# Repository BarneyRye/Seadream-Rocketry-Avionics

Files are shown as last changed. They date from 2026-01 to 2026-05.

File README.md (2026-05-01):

# Seadream Rocketry PCB and Code
 
 | Kicad files include schematic, pcb, extra symbols, footprints 3d files and also the production files for JLCPCB |
 |---------|
 | Included code written in Platform.io on VSCode, uses prebuilt libaries and freeRTOS, one task for sensor reading and audio, other task for writing to SD |

 *Exclaimer: Component libraries only usable on KiCAD 9!* </br></br>

 Follow us on [Instagram](https://www.instagram.com/seadreamrocketry/)

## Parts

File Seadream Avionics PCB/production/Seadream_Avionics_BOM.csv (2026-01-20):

Reference | Qty | Value | DNP | Exclude from BOM | Exclude from Board | Footprint | Datasheet | Description | Part NO.
C1,C3,C4,C5,C6,C7,C12,C13,C14 | 9 | 100nF |  |  |  | Capacitor_SMD:C_0402_1005Metric | https://jlcpcb.com/api/file/downloadByFileSystemAccessId/8579707269996871680 | CL05B104KO5NNNC | C1525
C2,C8,C9,C10 | 4 | 10uF |  |  |  | Capacitor_SMD:C_0603_1608Metric | https://jlcpcb.com/api/file/downloadByFileSystemAccessId/8579707107920437248 | CL10A106KP8NNNC | C19702
C11 | 1 | 22uF |  |  |  | Capacitor_SMD:C_0805_2012Metric | https://jlcpcb.com/api/file/downloadByFileSystemAccessId/8579706866429190144 | CL21A226MAQNNNE | C45783
C15 | 1 | 1uF |  |  |  | Capacitor_SMD:C_0402_1005Metric | https://jlcpcb.com/api/file/downloadByFileSystemAccessId/8579707174974914560 | CL05A105KA5NQNC | C52923
D1,D2,D3 | 3 | LED |  |  |  | LED_SMD:LED_0805_2012Metric | https://jlcpcb.com/api/file/downloadByFileSystemAccessId/8550724080677908480 | NCD0805R1 | C84256
J1,J3 | 2 | B2B-PH-K-S(LF)(SN) |  |  |  | Connector_JST:JST_PH_B2B-PH-K_1x02_P2.00mm_Vertical | https://jlcpcb.com/api/file/downloadByFileSystemAccessId/8588889744620572672 | B2B-PH-K-S(LF)(SN) | C131337
J2 | 1 | TYPE-C16PIN |  |  |  | 2FOOTPRINTS:SHOUHAN_TYPE-C_16PIN_2MD__073_ | https://jlcpcb.com/api/file/downloadByFileSystemAccessId/8588893971980423168 | TYPE-C16PIN | C393939
MICRO_SD1 | 1 | TF-01A |  |  |  | 2FOOTPRINTS:TF-01A | https://jlcpcb.com/api/file/downloadByFileSystemAccessId/8588894212661764096 | TF-01A | C91145
R1,R2,R11 | 3 | 10k |  |  |  | Resistor_SMD:R_0402_1005Metric | https://jlcpcb.com/api/file/downloadByFileSystemAccessId/8588881989415931904 | 0402WGJ0103TCE | C25531
R3,R4 | 2 | 4k7 |  |  |  | Resistor_SMD:R_0402_1005Metric | https://jlcpcb.com/api/file/downloadByFileSystemAccessId/8579705941367193600 | 0402WGF4701TCE | C25900
R5 | 1 | 330 |  |  |  | Resistor_SMD:R_0603_1608Metric | https://jlcpcb.com/api/file/downloadByFileSystemAccessId/8579706223213461504 | 0603WAF3300T5E | C23138
R7,R10 | 2 | 5k1 |  |  |  | Resistor_SMD:R_0402_1005Metric | https://jlcpcb.com/api/file/downloadByFileSystemAccessId/8579706036003409920 | 0402WGF5101TCE | C25905
R8,R9 | 2 | 220 |  |  |  | Resistor_SMD:R_0603_1608Metric | https://jlcpcb.com/api/file/downloadByFileSystemAccessId/8579706178210742272 | 0603WAF2200T5E | C22962
S1 | 1 | KMR221GLFS |  |  |  | 2FOOTPRINTS:SW_KMR221GLFS | https://jlcpcb.com/api/file/downloadByFileSystemAccessId/8588916370310369280 | KMR221GLFS | C72443
SW1 | 1 | SSSS810701 |  |  |  | 2FOOTPRINTS:SW-SMD_SSSS810701 | https://jlcpcb.com/api/file/downloadByFileSystemAccessId/8588917637593751552 | SSSS810701 | C97433
U1 | 1 | BMP280 |  |  |  | 2FOOTPRINTS:XDCR_BMP280 | https://jlcpcb.com/api/file/downloadByFileSystemAccessId/8588881905890156544 | BMP280 | C83291
U2 | 1 | ESP32-S3-MINI-1U-N8 |  |  |  | RF_Module:ESP32-S2-MINI-1U | https://documentation.espressif.com/esp32-s3-mini-1_mini-1u_datasheet_en.pdf | ESP32-S3-MINI-1U-N8 | C2980299
U3 | 1 | LSM6DSO32TR |  |  |  | 2FOOTPRINTS:XDCR_LSM6DSO32TR | https://jlcpcb.com/api/file/downloadByFileSystemAccessId/8588926227138138112 | LSM6DSO32TR | C1864162
U4 | 1 | LD1117S33TR |  |  |  | 2FOOTPRINTS:SOT230P700X180-4N | https://jlcpcb.com/api/file/downloadByFileSystemAccessId/8586198736901459968 | LD1117S33TR | C86781
U5 | 1 | SHT40-AD1B-R3 |  |  |  | 2FOOTPRINTS:SHT4X | https://jlcpcb.com/api/file/downloadByFileSystemAccessId/8588907595537399808 | SHT40-AD1B-R3 | C2848306
U6 | 1 | LD39200PU33R |  |  |  | 2FOOTPRINTS:SON95P300X300X100-7N | https://jlcpcb.com/api/file/downloadByFileSystemAccessId/8588886586771845120 | LD39200PU33R | C222192
U7 | 1 | MAX98357AETE_T |  |  |  | 2FOOTPRINTS:QFN50P300X300X80-17N | https://jlcpcb.com/api/file/downloadByFileSystemAccessId/8588886693302161408 | MAX98357AETE_T | C910544

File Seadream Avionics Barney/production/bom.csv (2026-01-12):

Designator | Footprint | Quantity | Value | LCSC Part #
C1, C12, C13, C14, C3, C4, C5, C6, C7 | 0402 | 9 | 100nF
C10, C2, C8, C9 | 0603 | 4 | 10uF
C11 | 0805 | 1 | 22uF
C15 | 0402 | 1 | 1uF
D1, D2, D3 | 0805 | 3 | LED
J1, J3 | JST_PH_B2B-PH-K_1x02_P2.00mm_Vertical | 2 | B2B-PH-K-S(LF)(SN)
J2 | SHOUHAN_TYPE-C_16PIN_2MD__073_ | 1 | C393939
MICRO_SD1 | TF-01A | 1 | C91145
R1, R11, R2 | 0402 | 3 | 10k
R10, R7 | 0402 | 2 | 5k1
R3, R4 | 0402 | 2 | 4k7
R5 | 0603 | 1 | 330
R8, R9 | 0603 | 2 | 220
S1 | SW_KMR221GLFS | 1 | KMR221GLFS
SW1 | SW-SMD_SSSS810701 | 1 | SSSS810701
U1 | XDCR_BMP280 | 1 | BMP280
U2 | ESP32-S2-MINI-1U | 1 | ESP32-S3-MINI-1U-N8
U3 | XDCR_LSM6DSO32TR | 1 | LSM6DSO32TR
U4 | SOT230P700X180-4N | 1 | LD1117S33TR
U5 | SHT4X | 1 | SHT40-AD1B-R3
U6 | SON95P300X300X100-7N | 1 | LD39200PU33R
U7 | QFN50P300X300X80-17N | 1 | MAX98357AETE_T

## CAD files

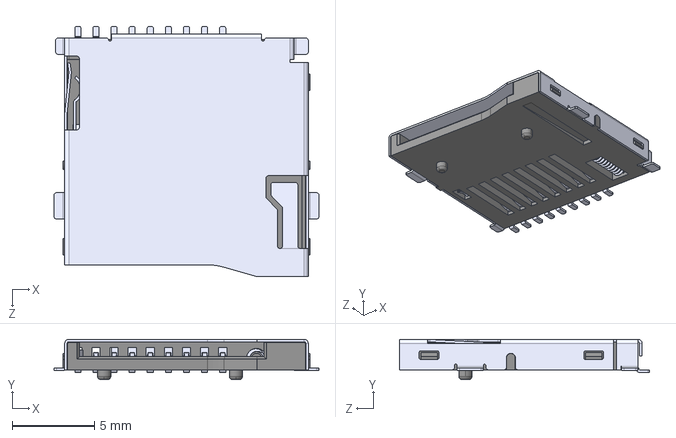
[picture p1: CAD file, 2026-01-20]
Seadream Avionics PCB/Parts/3D/TF-01A.step
16.1 x 2.45 x 15.2 mm

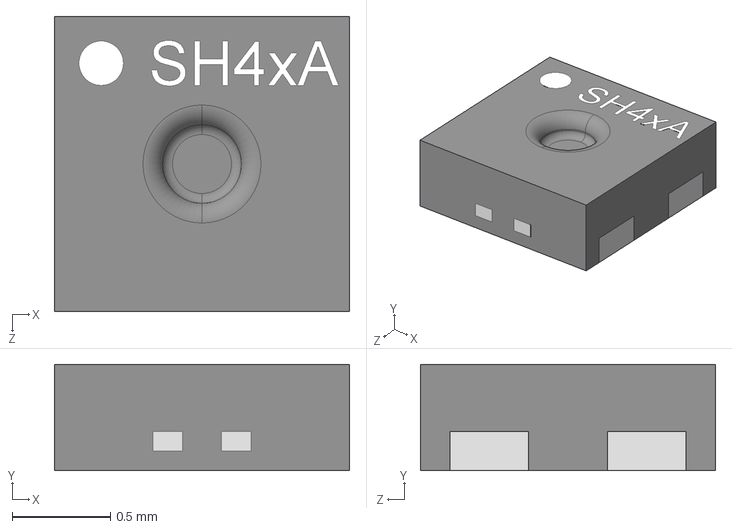
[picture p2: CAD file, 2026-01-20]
Seadream Avionics PCB/Parts/3D/SHT40-AD1B-R3.step
1.50 x 0.541 x 1.50 mm

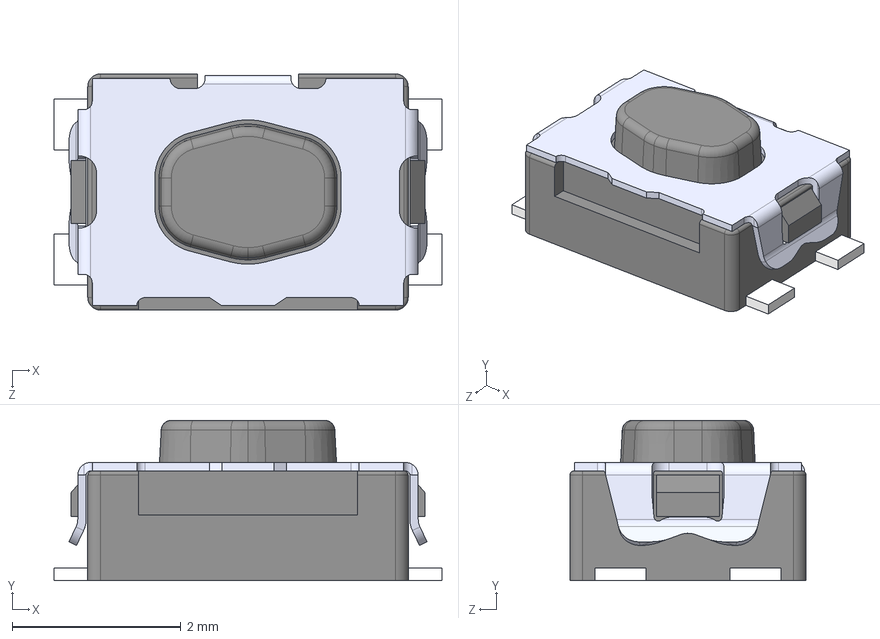
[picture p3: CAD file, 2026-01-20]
Seadream Avionics PCB/Parts/3D/KMR221GLFS.step
4.60 x 1.90 x 2.80 mm

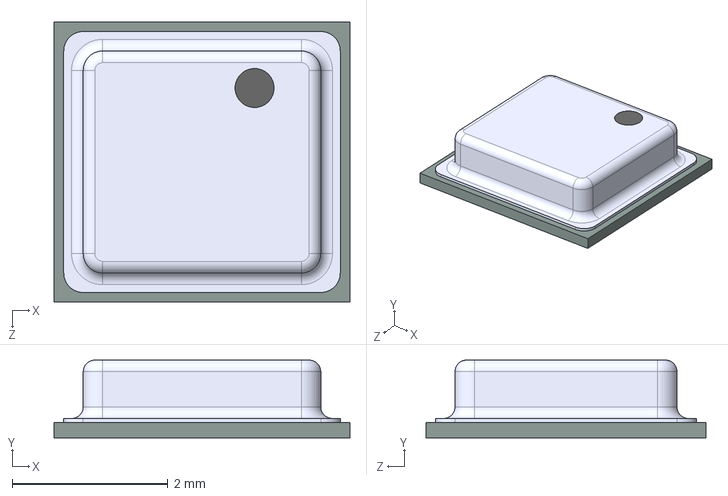
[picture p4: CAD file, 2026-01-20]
Seadream Avionics PCB/Parts/3D/BMP180.step
3.80 x 1.00 x 3.60 mm

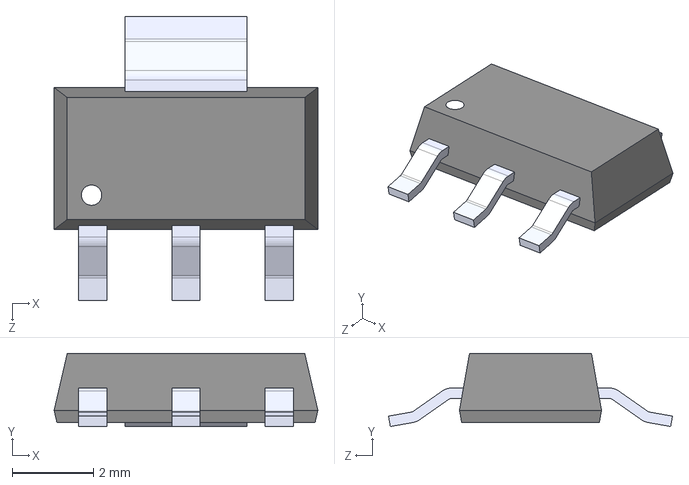
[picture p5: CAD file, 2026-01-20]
Seadream Avionics PCB/Parts/3D/LD1117S33TR.step
6.50 x 1.80 x 7.00 mm

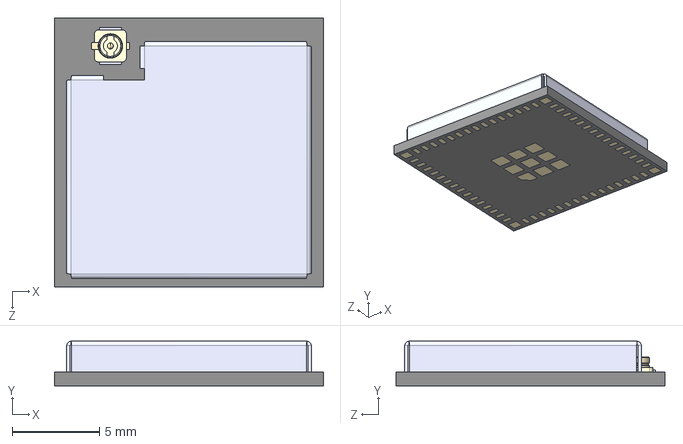
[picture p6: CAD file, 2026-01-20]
Seadream Avionics PCB/Parts/3D/ESP32-S3-MINI-1U-N8.step
15.4 x 2.55 x 15.4 mm
ESP32-S3-MINI-1U-N8_ESP32-C3-MINI-1-N4
antenna jack

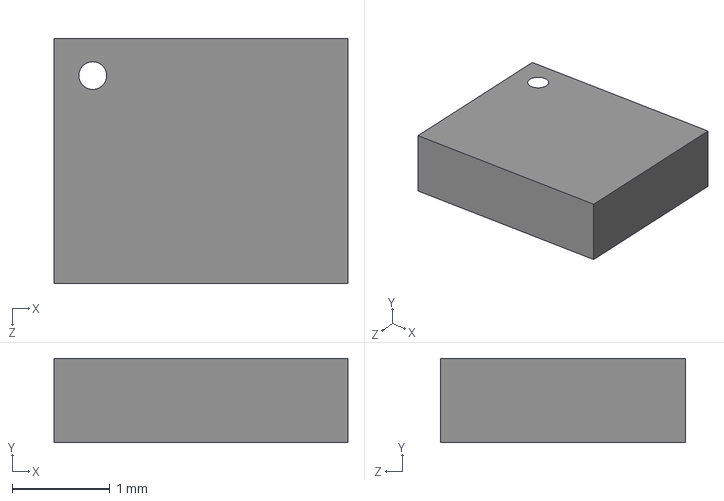
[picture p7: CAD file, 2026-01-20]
Seadream Avionics PCB/Parts/3D/LSM6DSO32TR.step
3.00 x 0.86 x 2.50 mm

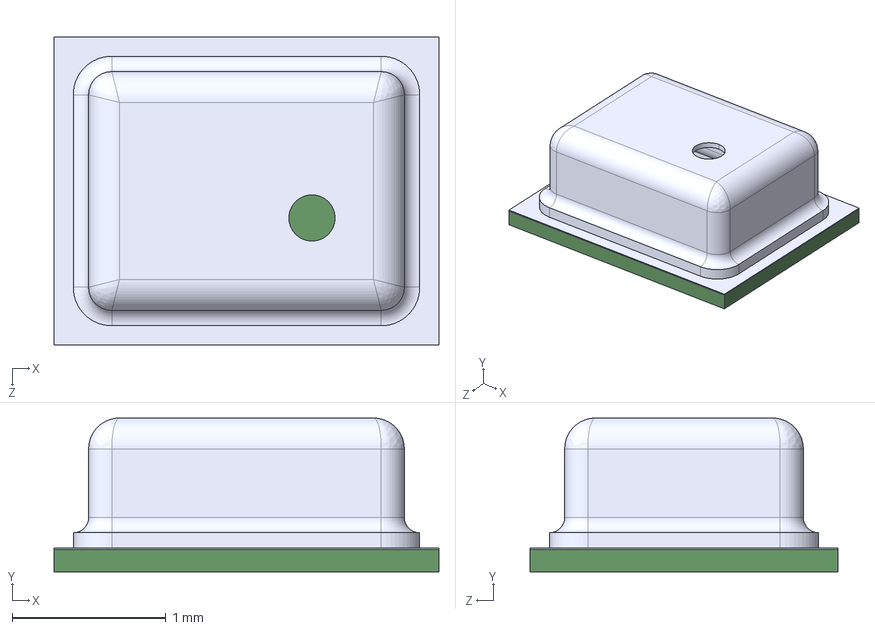
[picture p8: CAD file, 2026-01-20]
Seadream Avionics PCB/Parts/3D/BMP280.step
2.50 x 1.00 x 2.00 mm

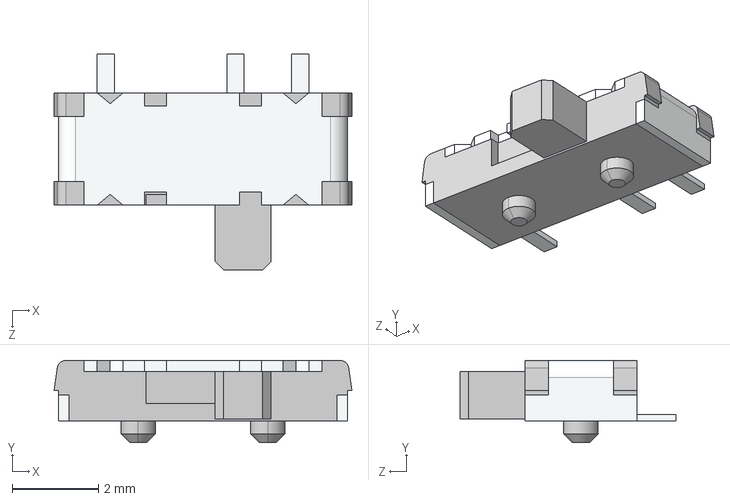
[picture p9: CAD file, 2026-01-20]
Seadream Avionics PCB/Parts/3D/SSSS810701.stp
6.90 x 1.90 x 5.00 mm

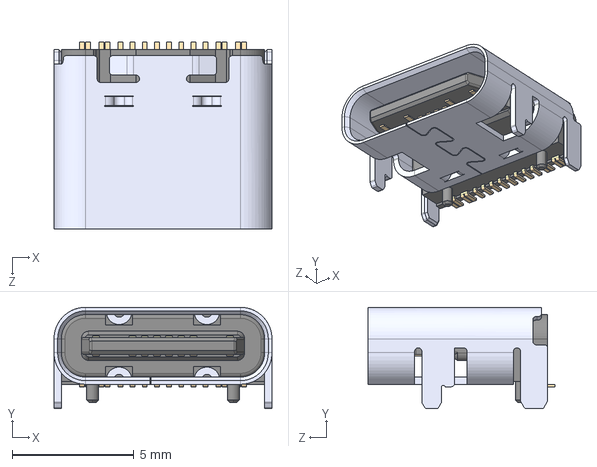
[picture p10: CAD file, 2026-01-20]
Seadream Avionics PCB/Parts/3D/TYPE-C_16PIN_2MD__073_.step
8.94 x 4.16 x 7.65 mm

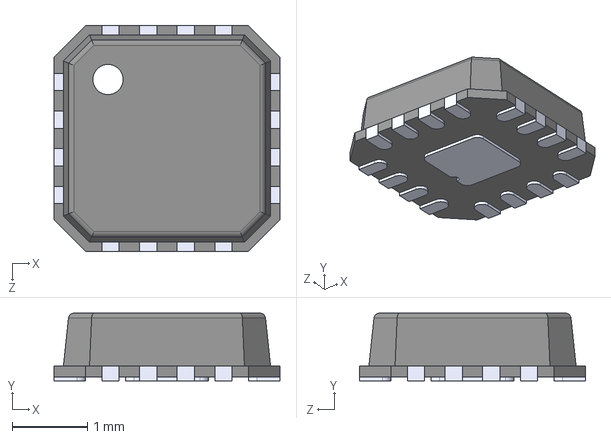
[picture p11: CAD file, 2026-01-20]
Seadream Avionics PCB/Parts/3D/MAX98357AETE_T.step
3.00 x 0.9 x 3.00 mm

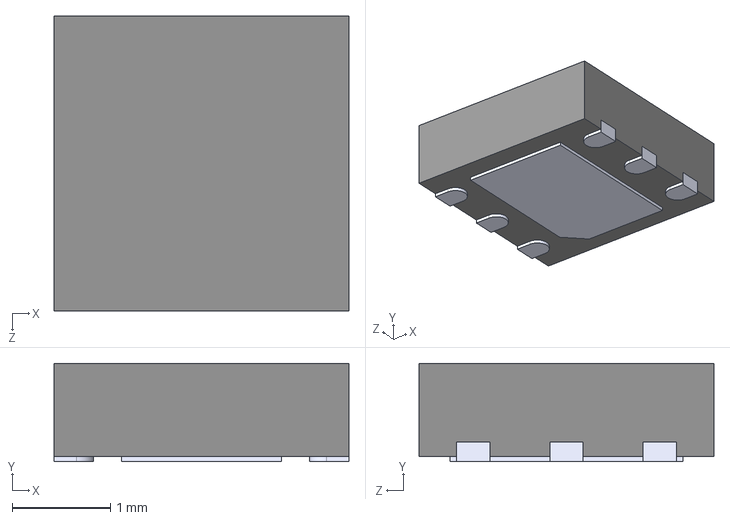
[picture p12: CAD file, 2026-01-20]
Seadream Avionics PCB/Parts/3D/LD39200PU33R.step
3.00 x 1 x 3.00 mm

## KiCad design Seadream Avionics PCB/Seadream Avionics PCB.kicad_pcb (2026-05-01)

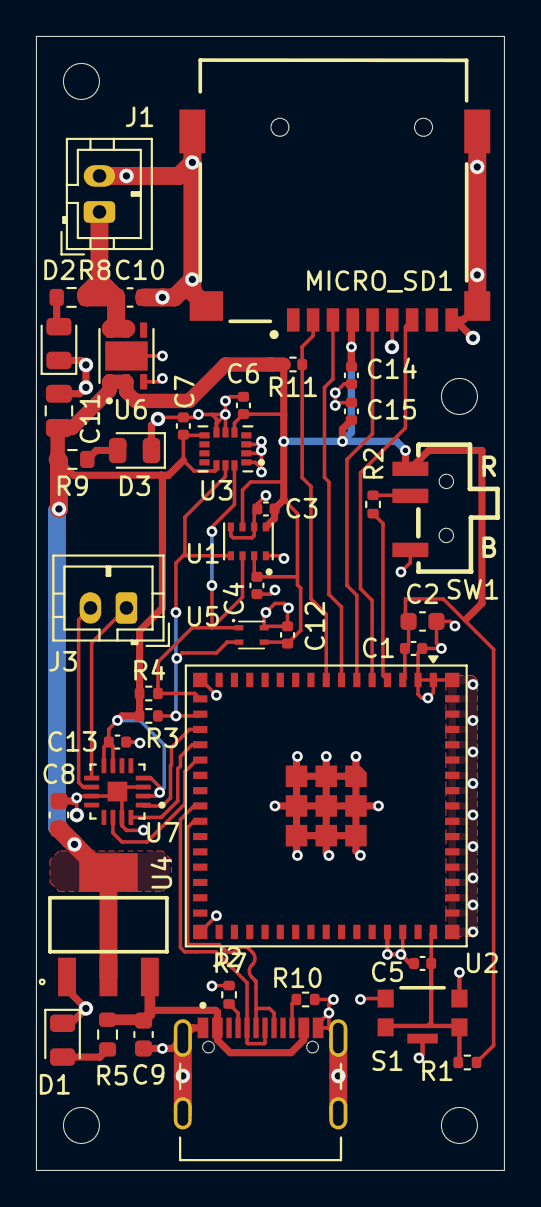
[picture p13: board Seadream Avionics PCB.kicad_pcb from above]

Board: 2 copper layers, 26.0 x 63.0 mm, 41 parts (0 on the bottom side), 25 nets.

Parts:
C1, C3, C4, C5, C6, C7, C12, C13, C14: 100nF; C_0402_1005Metric
C2, C8, C9, C10: 10uF; C_0603_1608Metric
C11: 22uF; C_0805_2012Metric
C15: 1uF; C_0402_1005Metric
D1, D2, D3: LED; LED_0805_2012Metric
J1, J3: B2B-PH-K-S(LF)(SN); JST_PH_B2B-PH-K_1x02_P2.00mm_Vertical
J2: TYPE-C16PIN; SHOUHAN_TYPE-C_16PIN_2MD__073_
MICRO_SD1: TF-01A
R1, R2, R11: 10k; R_0402_1005Metric
R3, R4: 4k7; R_0402_1005Metric
R5: 330; R_0603_1608Metric
R7, R10: 5k1; R_0402_1005Metric
R8, R9: 220; R_0603_1608Metric
S1: KMR221GLFS; SW_KMR221GLFS
SW1: SSSS810701; SW-SMD_SSSS810701
U1: BMP280; XDCR_BMP280
U2: ESP32-S3-MINI-1U-N8; ESP32-S2-MINI-1U
U3: LSM6DSO32TR; XDCR_LSM6DSO32TR
U4: LD1117S33TR; SOT230P700X180-4N
U5: SHT40-AD1B-R3; SHT4X
U6: LD39200PU33R; SON95P300X300X100-7N
U7: MAX98357AETE_T; QFN50P300X300X80-17N

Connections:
+3.3V: C1.2, C2.2, C3.1, C4.1, C6.1, C7.1, C8.1, C11.2, C12.1, C13.1, C14.2, C15.2, MICRO_SD1.4 (VDD), R1.2, R3.1, R4.1, R9.1, R11.1, SW1.3 (C), U1.2 (CSB), U1.6 (VDDIO), U1.8 (VDD), U2.3 (3V3), U3.5 (VDDIO), U3.8 (VDD), U3.12 (CS), U4.2 (OUT), U4.4 (OUT), U5.3 (VDD), U6.1 (OUT), U6.2 (SENSE), U7.2 (GAIN_SLOT), U7.4 (SD_MODE), U7.7 (VDD), U7.8 (VDD)
/BOOT: R2.2, U2.4 (IO0)
/CD: MICRO_SD1.2 (CD/DAT3), R11.2, U2.8 (IO4)
/D+: J2.A6 (DP1), J2.B6 (DP2), U2.24 (IO20)
/D-: J2.A7 (DN1), J2.B7 (DN2), U2.23 (IO19)
/EN: C5.2, R1.1, S1.1, S1.4, U2.45 (EN)
/IO12: R4.2, U1.3 (SDI), U2.16 (IO12), U3.14 (SDA), U5.1 (SDA)
/IO13: R3.2, U1.4 (SCK), U2.17 (IO13), U3.13 (SCL), U5.2 (SCL)
/IO14: U2.18 (IO14), U7.1 (DIN)
/IO15: U2.19 (IO15), U7.16 (BCLK)
/IO16: U2.20 (IO16), U7.14 (LRCLK)
/MISO: MICRO_SD1.7 (DAT0), U2.5 (IO1)
/MOSI: MICRO_SD1.3 (CMD), U2.7 (IO3)
/OUT+: J3.1, U7.9 (OUTP)
/OUT-: J3.2, U7.10 (OUTN)
/SCK: MICRO_SD1.5 (CLK), U2.6 (IO2)
/USB 5V: C9.1, J2.A4_B9 (VBUS_A), J2.B4_A9 (VBUS_B), R5.1, U4.3 (IN)
GND: C1.1, C2.1, C3.2, C4.2, C5.1, C6.2, C7.2, C8.2, C9.2, C10.1, C11.1, C12.2, C13.2, C14.1, C15.1, D1.1 (K), D2.1 (K), D3.1 (K), J1.2, J2.A1_B12 (GND_A), J2.B1_A12 (GND_B), J2.SH1 (SHIELD), J2.SH2 (SHIELD), J2.SH3 (SHIELD), J2.SH4 (SHIELD), MICRO_SD1.6 (VSS), MICRO_SD1.CD1 (CD), MICRO_SD1.MP1 (SHIELD), MICRO_SD1.MP2 (SHIELD), MICRO_SD1.MP3 (SHIELD), MICRO_SD1.MP4 (SHIELD), R7.1, R10.2, S1.2, S1.3, S1.5, SW1.1 (A), U1.1 (GND), U1.5 (SDO), U1.7 (GND), U2.1 (GND1), U2.2 (GND1), U2.42 (GND1), U2.43 (GND1), U2.46 (GND1), U2.47 (GND1), U2.48 (GND1), U2.49 (GND1), U2.50 (GND1), U2.51 (GND1), U2.52 (GND1), U2.53 (GND1), U2.54 (GND2), U2.55 (GND2), U2.56 (GND2), U2.57 (GND2), U2.58 (GND2), U2.59 (GND2), U2.60 (GND3), U2.62 (GND2), U2.63 (GND2), U2.64 (GND2), U2.65 (GND2), U3.1 (SDO/SA0), U3.2 (SDX), U3.3 (SCX), U3.6 (GND), U3.7 (GND), U4.1 (GND), U5.4 (VSS), U6.3 (GND), U6.7 (EXP), U7.3 (GND), U7.11 (GND), U7.15 (GND), U7.17 (EP)
unnamed: D1.2 (A), R5.2
unnamed: D2.2 (A), R8.2
unnamed: D3.2 (A), R9.2
unnamed: C10.2, J1.1, R8.1, U6.5 (EN), U6.6 (IN)
unnamed: J2.A5 (CC1), R7.2
unnamed: J2.B5 (CC2), R10.1
unnamed: R2.1, SW1.2 (B)

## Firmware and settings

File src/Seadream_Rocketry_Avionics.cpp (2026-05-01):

//If working in arduino IDE, to allow use of esp32 boards
//https://espressif.github.io/arduino-esp32/package_esp32_index.json
//File->Preferences->Additional Board Manager URLs
//Boards Manager -> esp32 by espressif Systems
//Board->ESP32S3 DEV module


//Libaries used and need installing:
/*
Adafruit_LSM6DS
Adafruit SHT4x and dependencies
Adafruit BMP280
*/


//Includes for added libaries
#include <Arduino.h> //Base arduino libary if not using arduino IDE
#include <Wire.h> //I2C protocols
#include <Adafruit_Sensor.h> //Base sensor libary for Adafruit libaries
#include <Adafruit_SHT4x.h> //Temperature and Humidity sensor libaries
#include <Adafruit_LSM6DSO32.h>//Accelerometer and Gyro libary
#include <Adafruit_BMP280.h>//Barometer libary
#include <SD.h> //SD card libary
#include <SPI.h> //SPI libary
#include <FreeRTOS.h> //FreeRTOS base libary to allow for multitasking
#include <queue.h> //FreeRTOS queue libary for inter-task communication

//Config pins
#define I2C_SDA 12 //I2C pins
#define I2C_SCL 13
#define SPI_SCK 2 //SPI/SD card pins
#define SPI_MOSI 3
#define SPI_MISO 1
#define SPI_CS 4

//Log Rates
#define initial_log_rate 50    // Hz, initial logging rate
#define final_log_rate 10      // Hz, reduced logging rate for decent/slower speeds
#define reduce_Hz_time 60      // s, time after which to reduce logging rate after apogee
#define MAX_BUFFER_LINES 5     // No. of data logs per buffer
#define MAX_BUFFER_LENGTH 150  // Length of char buffer lines

//Object creating from libaries
Adafruit_SHT4x sht4 = Adafruit_SHT4x(); //Temperature and Humidity sensor
Adafruit_LSM6DSO32 imu; //Accelerometer and Gyro
Adafruit_BMP280 bmp; //Barometer

//Data Struct
typedef struct { //struct to store sensor data
  uint32_t time; //TIme of log in ms
  float humidity; //Humidity in %
  float temp_sens; //Temp in C from SHT4x
  float temp_bmp; //Temp in C from BMP280
  float pressure; //Pressure in kPa from BMP280
  float altitude; //Altitude in M from BMP280
  float ax; //Acceleration X in m/s^2
  float ay; //Acceleration Y in m/s^2
  float az; //Acceleration Z in m/s^2
  float gx; //Gyro X in deg/s
  float gy; //Gyro Y in deg/s
  float gz; //Gyro Z in deg/s
} data_struct;

//FreeRTOS Queue
QueueHandle_t logQueue;

//SD Log Filename
char logFilename[15];

//Double Buffers for data logging
data_struct buffer1[MAX_BUFFER_LINES]; // Array of structs to hold data buffers
data_struct buffer2[MAX_BUFFER_LINES];
bool useBuffer1 = true;   // Active buffer flag
uint8_t bufferIndex = 0;  // Index for current buffer

//COnnection Flags
bool SD_connected = false; //SD card connection flag
bool imu_connected = false; //IMU connection flag
bool bmp_connected = false; //BMP280 connection flag
bool sht4_connected = false; //SHT4x connection flag

//Fuunction Prototypes
void getNextLogFilename(char* name); //Generate next log filename if log1.csv exists, make log2.csv etc
void getData(data_struct *data_buffer); //Read sensors and fill data struct
void getBufferLine(char *line, data_struct data_buffer); //Converts data struct to string line for block writing to SD card
void char_buffer_write(uint8_t count, data_struct data_buffer, char data_char_buffer[][MAX_BUFFER_LENGTH]); //Writes line to array of char buffers
void logRate_reduce(uint32_t *log_rate, bool *reduced, bool apogee); //Checks if it's time to reduce log rate and reduces it
void takeoff_detection(bool *takeoff, float initial_altitude); //Detects takeoff based on accelerometer data
void apogee_detection(bool *apogee, bool takeoff); //Detects apogee based on altitude data

//FreeRTOS Tasks
void SensorTask(void *pvParameters); //Core 1 to handle sensor reading
void LoggingTask(void *pvParameters); //Core 0 to handle logging data to SD card

//Setup
void setup() {
  Serial.begin(115200); //Begin serial communication
  delay(1000); //Wait for serial to initialise
  Serial.println(F("Initialising...")); //Print initialising message

  //I2C
  Wire.begin(I2C_SDA, I2C_SCL); //Connect I2C to specified pins
  Wire.setClock(400000); //Set I2C clock frequency to 400kHz
  delay(1000); //Wait for I2C to stabilise

  //SPI
  SPI.begin(SPI_SCK, SPI_MISO, SPI_MOSI); //Begin SPI for SD card

  //Accelerometer and Gyro
  if (!imu.begin_I2C()) {Serial.println(F("Failed to find Accelerometer")); } //Begins I2C connection to Accel/Gyro, if fails, print failure to serial
  else {
    imu.setAccelDataRate(LSM6DS_RATE_833_HZ); //Sets accelerometer data rate to 52Hz
    imu.setAccelRange(LSM6DSO32_ACCEL_RANGE_32_G); //Sets accelerometer range to 32G
    imu.setGyroDataRate(LSM6DS_RATE_833_HZ); //Sets gyro data rate to 52Hz
    imu.setGyroRange(LSM6DS_GYRO_RANGE_2000_DPS); //Sets gyro range to 2000 degrees per second
    imu_connected = true; //Sets IMU connected flag to true
    Serial.println(F("Accelerometer found")); //Prints success message to serial
  }
  
  //Barometer
  if (!bmp.begin(0x77)) { Serial.println(F("Failed to find Barometer")); } //Begins I2C connection to Barometer, if fails, print failure to serial
  else{
    bmp.setSampling(Adafruit_BMP280::MODE_NORMAL,
                    Adafruit_BMP280::SAMPLING_X1,
                    Adafruit_BMP280::SAMPLING_X1,    
                    Adafruit_BMP280::FILTER_OFF,  
                    Adafruit_BMP280::STANDBY_MS_1); 
    bmp_connected = true; //Sets BMP280 connected flag to true#
    Serial.println(F("Barometer found")); //Prints success message to serial
  }
  //Temperature and Humidity Sensor
  if (!sht4.begin(&Wire)) { Serial.println(F("Temperature/Humidity sensor not found")); } //Begins I2C connection to Temp/Humidity sensor, if fails, print failure to serial
  else {
    sht4_connected = true; //Sets SHT4x connected flag to true
  
  }
  //SD CARD
  if (!SD.begin(SPI_CS)) { //Begins SD card connection, if fails, print failure to serial
    Serial.println(F("SD Card not found"));
  } 
  else {
    getNextLogFilename(logFilename); //Get next available log filename
    Serial.print(F("Log file: ")); Serial.println(logFilename); //Prints log filename to serial
    File f = SD.open(logFilename, FILE_WRITE); //Opens/creates file for writing
    if (f) { //If file opened successfully
      //Write CSV header line
      f.println("Time_ms,Humidity_%,Temp_C,Temp_BMP_C,Pressure_kPa,Altitude_M,Accel_X,Accel_Y,Accel_Z,Gyro_X,Gyro_Y,Gyro_Z");
      f.close(); //Closes file
      SD_connected = true; //Sets SD connected flag to true
      Serial.println(F("Log file created")); //Prints success message to serial
    } else {
      Serial.println(F("Failed to open log file")); //Prints failure message to serial
    }
  }

  //FreeRTOS Queue
  logQueue = xQueueCreate(2, sizeof(bool)); //Create queue to hold 2 buffer ready flags

  //Create FreeRTOS Tasks
  xTaskCreatePinnedToCore(SensorTask, "SensorTask", 4096, NULL, 1, NULL, 1);  // Core 1 for sensors and audio
  xTaskCreatePinnedToCore(LoggingTask, "LoggingTask", 4096, NULL, 1, NULL, 0);          // Core 0 for logging

  Serial.println(F("Finished Initialising")); //Print finished initialising message
}

//Loop
void loop() {
  //Nothing here, all handled by FreeRTOS tasks
}
//Sensor and Audio Task
void SensorTask(void *pvParameters) {
  static bool takeoff = false; //Takeoff detected flag
  static bool apogee = false; //Apogee detected flag
  static bool landed = false; //Landed flag
  static uint32_t log_rate = 1000 / initial_log_rate; //Sets initial log rate in ms, converts from Hz
  static bool reduced = false; //Log rate reduced flag
  static uint32_t last_log = 0; //Last log time
  static float initial_altitude = 0.0f; //Initial altitude at startup, used for takeoff detection, value gotten after first data colelction
  static bool first_run = false; //Flag to indicate first run of data collection got intial altitude
  static uint32_t loop_start = millis(); //Loop start time

  for (;;) { //Infinite loop for task

    //Apogee Detection
    if (!apogee) apogee_detection(&apogee, takeoff); //If apogee not detected yet, call apogee detection function to update apogee flag

    //Log Rate Reduction
    if (!reduced) logRate_reduce(&log_rate, &reduced, takeoff); //If log rate hasn't been reduced yet, check if it's time to reduce it and reduce if so
     
    //Data Logging
    if (millis() - last_log >= log_rate && !landed) { //If it's time to log data, i.e. time since last log >= log rate and not landed
      uint32_t now = millis(); //Time for current logging iteration
      static uint32_t data_start = now; //First data log time
      
      //Read Sensors and fill data struct
      data_struct data; //Create data struct for current iteration
      data.time = now - data_start; //Stores time since start in data struct
      getData(&data); //Fills data struct with sensor data using function

      last_log = now; //Sets last log time to now

      //Print data to serial for debugging
      /*
      Serial.print("Time: "); Serial.print(data.time);
      Serial.print(" ms, Humidity: "); Serial.print(data.humidity); Serial.print(" %, Temp: "); Serial.print(data.temp_sens); Serial.print(" C");
      Serial.print(", Temp_BMP: "); Serial.print(data.temp_bmp); Serial.print(" C, Pressure: "); Serial.print(data.pressure); Serial.print(" kPa, Altitude: "); Serial.print(data.altitude); Serial.print(" m");
      Serial.print(", Accel (m/s^2): X "); Serial.print(data.ax); Serial.print(" Y "); Serial.print(data.ay); Serial.print(" Z "); Serial.print(data.az);
      Serial.print(", Gyro (deg/s): X "); Serial.print(data.gx); Serial.print(" Y "); Serial.print(data.gy); Serial.print(" Z "); Serial.println(data.gz); 
      */

      //CSV format for easy import to analysis software
      /*
      Serial.print(data.time); Serial.print(","); 
      Serial.print(data.humidity); Serial.print(","); 
      Serial.print(data.temp_sens); Serial.print(","); 
      Serial.print(data.temp_bmp); Serial.print(",");
      Serial.print(data.pressure); Serial.print(","); 
      Serial.print(data.altitude); Serial.print(","); 
      Serial.print(data.ax); Serial.print(","); 
      Serial.print(data.ay); Serial.print(","); 
      Serial.print(data.az); Serial.print(","); 
      Serial.print(data.gx); Serial.print(","); 
      Serial.print(data.gy); Serial.print(","); 
      Serial.println(data.gz);
      */
      if (SD_connected) { //If SD card connected, proceed to buffer data for logging
        //Fill active buffer
        if (useBuffer1) { //If flag is true, fill buffer1
          buffer1[bufferIndex] = data; //Copy data struct to buffer1 at current index
        } else { //Else fill buffer2
          buffer2[bufferIndex] = data; //Copy data struct to buffer2 at current index
        }
        bufferIndex++; //Increases buffer index

        //If buffer full, send to logging task
        if (bufferIndex >= MAX_BUFFER_LINES) { //If buffer index >= max buffer lines and SD card connected
          bool readyBuffer = useBuffer1;  // Sets flag for which buffer is ready
          xQueueSend(logQueue, &readyBuffer, portMAX_DELAY); //Sends ready buffer flag to logging task
          bufferIndex = 0; //Resets buffer index
          useBuffer1 = !useBuffer1;  //Swap active buffer to fill
        }
      }
      
      else {
        Serial.println(F("SD Card not connected, skipping logging")); //If SD card not connected, print message to serial
        static uint8_t sd_reconnect_attempts = 0; //Counter for SD reconnect attempts
        if (sd_reconnect_attempts > 10) {
          if (SD.begin(SPI_CS)) { //Try to reconnect to SD card
            SD_connected = true; //If successful, set SD connected flag to true
            Serial.println(F("SD Card reconnected")); //Print reconnection message to serial
          }
          sd_reconnect_attempts = 0; //Reset reconnect attempts counter
        }
        sd_reconnect_attempts++; //Increase reconnect attempts counter
      }

      initial_altitude = data.altitude; //Initial altitude at startup
      first_run = true;
    }

    if (!takeoff && first_run) { //Calls takeoff detection function to update takeoff flag
      takeoff_detection(&takeoff, initial_altitude);
      loop_start = millis(); //Reset loop start time untill takeoff detected
    }
    vTaskDelay(1);  //Yield to other tasks
  }
}

//Logging Task
void LoggingTask(void *pvParameters) {
  char data_char_buffer[MAX_BUFFER_LINES][MAX_BUFFER_LENGTH]; //Char buffer array for block writing to SD card

  for (;;) { //Infinite loop for task
    bool readyBuffer; //Variable to hold which buffer is ready
    if (xQueueReceive(logQueue, &readyBuffer, portMAX_DELAY) == pdPASS) { //Waits for ready buffer flag from sensor task
      data_struct *buffer = readyBuffer ? buffer1 : buffer2; //if readyBuffer is true, use buffer1, else use buffer2

      //Convert data structs to char buffer lines
      for (uint8_t i = 0; i < MAX_BUFFER_LINES; i++) { //Loops between buffer lines
        char_buffer_write(i, buffer[i], data_char_buffer); //Converts struct data lines to char buffer lines and inserts into corressponding index
      }

      //Write char buffer lines to SD card
      File f = SD.open(logFilename, FILE_APPEND); //Opens log file for appending
      if (f) { //If file opened successfully
        for (uint8_t i = 0; i < MAX_BUFFER_LINES; i++) { //Loops between buffer lines
          f.println(data_char_buffer[i]); //Writes char buffer line to file
        }
        f.close(); //Closes file
      }
    }
  }
}

//Helper Functions
void getNextLogFilename(char *name) { //Gets next available log filename
  uint8_t index = 1; //Starts at log1.csv
  char temp_name[15]; //Temporary filename storage
  while (true) { //Infinite loop until available filename found, doesn't slow logging as done before looping starts
    sprintf(temp_name,"/log%d.csv",index); //Creates filename string from index
    if (!SD.exists(temp_name)){ //If file doesn't exist, copy to output and return
      strcpy(name, temp_name); //Copy temporary name to output
      return; //Exit function
    }
    index++; //Increase index and try again
  }
}

void takeoff_detection(bool *takeoff, float initial_altitude) { //Detects takeoff based on accelerometer data
  if (useBuffer1){
    if (buffer1[bufferIndex].altitude - initial_altitude > 10){ //If altitude has increased by more than 10m since start
      *takeoff = true; //Sets takeoff flag to true
    }
  }
  else{
    if (buffer2[bufferIndex].altitude - initial_altitude > 10){ //If altitude has increased by more than 10m since start
      *takeoff = true; //Sets takeoff flag to true
    }
  }
}

void apogee_detection(bool *apogee, bool takeoff) { //Detects apogee based on altitude data
  if (!takeoff) return; //If takeoff not detected, exit function
  static uint32_t period_start = millis(); //Start time for apogee detection period
  static float start_altitude = 0.0f; //Altitude at start of apogee detection period
  if (period_start - millis() >= 5000) { //If 5 seconds have passed since start of period
    if (useBuffer1){
      if (buffer1[bufferIndex].altitude < start_altitude){ //If altitude has decreased since start of period
        *apogee = true; //Sets apogee flag to true
      }
    }
    else{
      if (buffer2[bufferIndex].altitude < start_altitude){ //If altitude has decreased since start of period
        *apogee = true; //Sets apogee flag to true
      }
    }
    start_altitude = buffer1[bufferIndex].altitude; //Updates start altitude for next period
    period_start = millis(); //Resets period start time
  }
}

void landing_detection(bool *landed, bool takeoff, bool apogee) { //Detects landing based on altitude data
  if (!takeoff || !apogee) return; //If takeoff or apogee not detected, exit function
  static uint32_t apogee_time = 0; //Time of apogee detection
  if (apogee && apogee_time == 0) { //If apogee detected
    apogee_time = millis(); //Sets apogee time to current time
  }
  if (millis() - apogee_time < 60000) return; //If it's been less than 60 seconds since apogee, exit function, prevents false landing detection during decent
  static uint32_t period_start = millis(); //Start time for landing detection period
  static float start_altitude = 0.0f; //Altitude at start of landing detection period
  if (period_start - millis() >= 10000) { //If 10 seconds have passed since start of period
    if (useBuffer1){
      if (buffer1[bufferIndex].altitude > start_altitude - 5){ //If altitude has decreased to within 5m of start altitude since start of period
        *landed = true; //Sets landed flag to true
      }
    }
    else{
      if (buffer2[bufferIndex].altitude > start_altitude - 5){ //If altitude has decreased to within 5m of start altitude since start of period
        *landed = true; //Sets landed flag to true
      }
    }
    start_altitude = buffer1[bufferIndex].altitude; //Updates start altitude for next period
    period_start = millis(); //Resets period start time
  }
}

void logRate_reduce(uint32_t *log_rate, bool *reduced, bool apogee) { //Checks if it's time to reduce log rate and reduces it
  if (!apogee) return; //If apogee not detected, exit function
  static uint32_t apogee_time = 0; //Time of apogee detection
  if (apogee && apogee_time == 0) { //If apogee detected
    apogee_time = millis(); //Sets apogee time to current time
  }
  if ((millis() - apogee_time >= (reduce_Hz_time * 1000)) && apogee) { //If time since apogee >= reduce time
    *log_rate = 1000 / final_log_rate; //Sets log rate to final log rate in ms, converts from Hz
    *reduced = true; //Sets reduced flag to true
  }
}

void getData(data_struct *data_buffer) { //Reads sensors and fills data struct
  //Accelerometer and Gyro
  if (!imu_connected) { //If IMU not connected, fill with zeros
    data_buffer->ax = 0.0f;
    data_buffer->ay = 0.0f;
    data_buffer->az = 0.0f;
    data_buffer->gx = 0.0f;
    data_buffer->gy = 0.0f;
    data_buffer->gz = 0.0f;
  }
  else {
    sensors_event_t accel, gyro, temp_imu; //Create sensor event structs
    imu.getEvent(&accel, &gyro, &temp_imu); //Reads sensor data into structs
    data_buffer->ax = accel.acceleration.x; //Fills data struct with accel and gyro data
    data_buffer->ay = accel.acceleration.y;
    data_buffer->az = accel.acceleration.z;
    data_buffer->gx = gyro.gyro.x;
    data_buffer->gy = gyro.gyro.y;
    data_buffer->gz = gyro.gyro.z;
  }

  //Barometer
  if (!bmp_connected) { //If BMP280 not connected, fill with zeros
    data_buffer->temp_bmp = 0.0f;
    data_buffer->pressure = 0.0f;
    data_buffer->altitude = 0.0f;
  }
  else {
    data_buffer->temp_bmp = bmp.readTemperature(); //Reads data from BMP280 and fills data struct
    data_buffer->pressure = bmp.readPressure() / 1000; //Convert Pa to kPa
    data_buffer->altitude = bmp.readAltitude(1013.25); //Assumes sea level pressure of 101325 Pa
  }

  //Temperature and Humidity Sensor
  if (!sht4_connected) { //If SHT4x not connected, fill with zeros
    data_buffer->humidity = 0.0f;
    data_buffer->temp_sens = 0.0f;
    return;
  }
  else {
    sensors_event_t humidity, temp; //Create sensor event structs
    sht4.getEvent(&humidity, &temp); //Reads sensor data into structs
    data_buffer->humidity = humidity.relative_humidity; //Fills data struct with temp and humidity data
    data_buffer->temp_sens = temp.temperature;
  }
}

void getBufferLine(char *line, data_struct data_buffer) { //Converts data struct to string line for block writing to SD card
  snprintf(line, MAX_BUFFER_LENGTH, //line is where the string is stored, MAX_BUFFER_LENGTH is max length of line
    "%lu,%.2f,%.2f,%.2f,%.2f,%.2f,%.3f,%.3f,%.3f,%.3f,%.3f,%.3f", //Format string for CSV line, with 2 decimal places for floats except 3 for accel/gyro
    data_buffer.time, //Corressponding data struct values to store in line
    data_buffer.humidity,
    data_buffer.temp_sens,
    data_buffer.temp_bmp,
    data_buffer.pressure,
    data_buffer.altitude,
    data_buffer.ax,
    data_buffer.ay,
    data_buffer.az,
    data_buffer.gx,
    data_buffer.gy,
    data_buffer.gz);
}

void char_buffer_write(uint8_t count, data_struct data_buffer, char data_char_buffer[][MAX_BUFFER_LENGTH]) { //Writes line to array of char buffers
  char line[MAX_BUFFER_LENGTH]; //Temporary line buffer
  getBufferLine(line, data_buffer); //Gets data line from data struct
  strcpy(data_char_buffer[count], line); //Copies line to char buffer array at specified index
}

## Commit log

2025-12-30 Added comments and moved some initial start times with millis
2026-01-12 Fixed issue with indexing in takeoff_detection function
    [Seadream_Rocketry_RTOS.cpp]
2026-01-12 Altitude detection bug fix
    [Seadream_Rocketry_RTOS.cpp]
2026-01-14 Updated PCB files
    [Seadream Avionics Barney.kicad_pcb, Seadream Avionics Barney.kicad_sch]
2026-01-14 Corrected pin defines
2026-01-14 Schematic Update
    [Seadream Avionics Barney.kicad_sch]
2026-01-20 Added £D file of PCB
2026-01-20 Renamed Files
    [BMP180.step, BMP280.step, ESP32-S3-MINI-1U-N8.step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]
2026-01-26 Added SD reconnect and connection flags
    [positions.csv]
2026-01-26 Quick edit
    [positions.csv]
2026-04-22 Update README with compatibility note for KiCAD
    Added a note about component libraries compatibility.
